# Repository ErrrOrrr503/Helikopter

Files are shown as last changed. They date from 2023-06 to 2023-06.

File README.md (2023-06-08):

# Helikopter
Еще один самособранный дрон. Цели: стабильный полет и потенциально большая грузоподъемность. Например, для поднятия фотоаппаруры.

# Комплектующие
Приобретались на aliexpress
* Рама: HSKRC XL9, карбоновая, X - образная


* Полетный контроллер: MATEKSYS H743-WING V2


* Контроллер двигателей ESC: Hobbywing XRotor Micro 60A 4 в 1 BLHeli-32


* GNSS & компас: MATEKSYS M10Q-5883


* Приемник и пульт: FLYSKY iA10B + FLYSKY i6x.


* АКБ: HRB LiPo 4S 3300mah 60C XT60, ширина ровно по раме.


* Винты: Карбоновые APC 1047, 10 дюймов хорошо встают не смотря на то что рама под 9 дюймовые


* Двигатели 2212 920KW


* FPV: 1200TVL камера + EWRF e708TM3 600mW передатчик + Skydroid 5.8G dual receier


* Шасси для F450 рамы: не использовалось, для XL9 слишком большое и тяжелое, использовались только углепластиковые трубки


* Провода 0.75 квадрата: соединение движков с ESC

* Провода ~3 квадрата: силовая проводка АКБ - ESC

* Тонкие провода в ассортименте

* Термоусадка в ассортименте

# Инструментарий
* 3D принтер Creality Ender 3 S1 Pro + PLA
* Паяльник
* Кусачки, отвертки и др. различный инструмент
* Прямые (мы надеемся) руки

# Проектирование

Для проектирования деталей использовались Solidworks и FreeCAD.
Проблем это как правило не составляло, за исключением 2х часов поиска причины не сходившегося чертежа из-за недоопределения вспомогательной геометрии.



# Изготовление

**Крепление камеры**

В комплекте рамы были приспособления для закрепления камеры. Однако в силу своей геометрии они не подходили к нашей камере. Поэтому для них была сделана замена. Точно подобрать размеры, чтобы крепления крепко зажималось но не оставляло зазоров получилось не сразу.



**Антенны**

Для закрепления антенн приема управляющего сигнала, передачи видеоизображения и антенны GNSS были изготовлены стойки. При их разработке ставилась задача максимально возможного удаления антенн друг от друга для снижения возможного взаимного влияния.





Первая версия крепления передатчика видео была спроектирована неправильно: вывод провода был с неправильной стороны - пришлось переделывать.

**Винты**

Имеющиеся двигатели и лопасти не подходили друг к другу. Большой проблемой было то, что диаметр отверстия лопасти был больше диаметра вала двигателя на ~0.2мм. Сделать втулку под такие размеры крайне проблематично. После исследования различных вариантов для ликвидации зазора была выбрана термоусадка. Процесс установки лопастей является относительно трудоемким для повторения и не был отснят, поэтому подробной фотографии нет.

**Пайка**

Довольно трудоемким был процесс разводки и пайки проводов для соединения компонентов между собой. Основную сложность составляли очень ограниченные размеры и геометрия, диктуемые рамой беспилотника.



**Программная часть**

В качестве прошивки используется Ardupilot c открытым исходным кодом. Ardupilot поддерживает используемый полетный контроллер, потребовалось только прошить бинарный файл во внутреннюю память. Ardupilot работает в паре с компьютерным ПО для настройки. Мы использовали MissionPlanner. Ardupilot имеет подробную документацию к настройкам и инструкции. Настройку можно производить в отведенных секциях или в сводной таблице параметров (там мы отключали логгирование т. к. иначе невозможен запуск без sd карты).



В пульте потребовалось инвертировать 2й канал т. к. движение вперед-назад было инвертировано.



**Шасси**
Все навесное оборудование расположено выше днища, так что без шасси можно было обойтись. Но в целях возможности размещения подвеса оно было сделано. Шасси съемное.



# Демонстрация

https://github.com/ErrrOrrr503/Helikopter/assets/55430721/89c44561-e986-4346-b0d1-1448f5957693

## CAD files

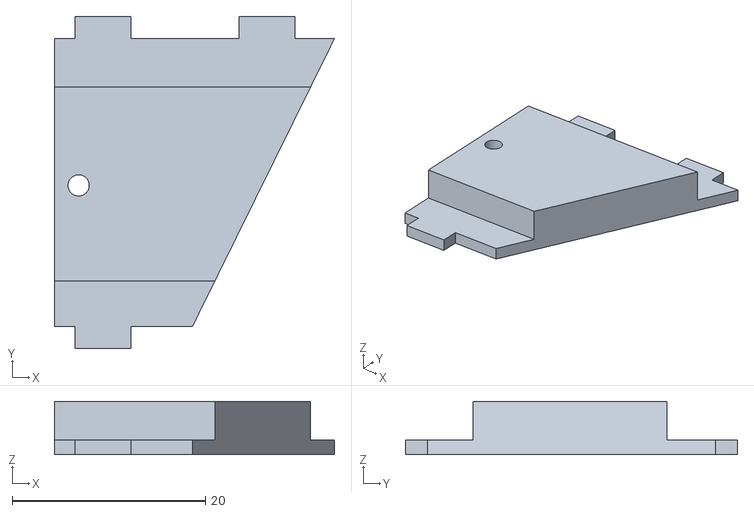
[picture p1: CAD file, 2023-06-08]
drafts/Cam_holder_right.stl
29.0 x 34.4 x 5.50

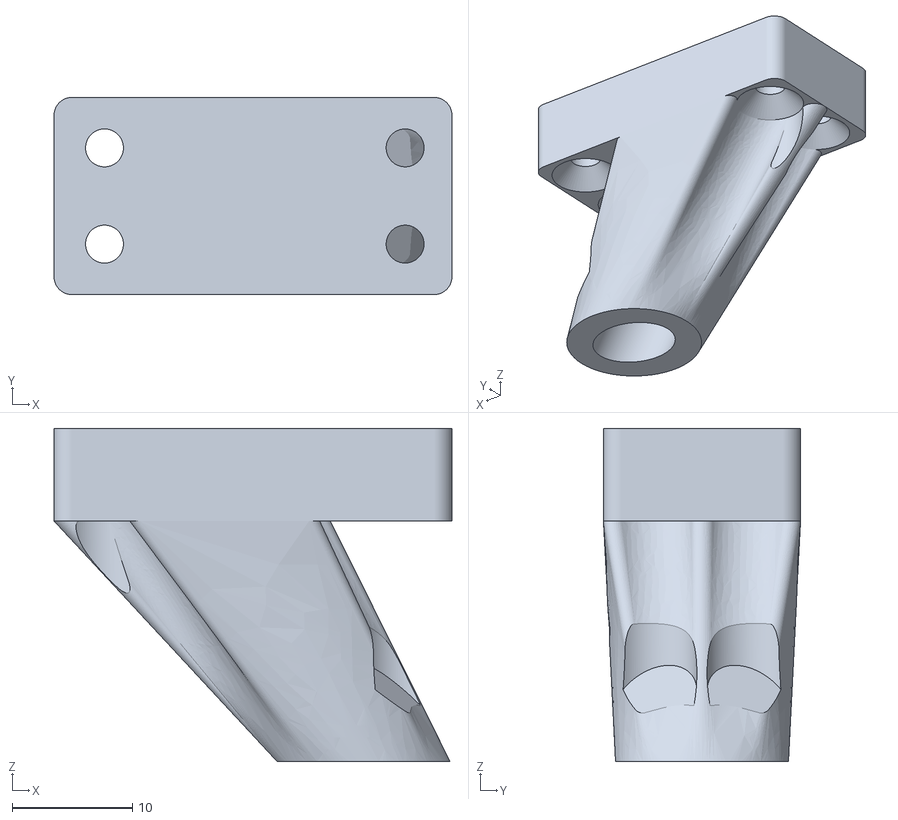
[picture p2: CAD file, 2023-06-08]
drafts/Leg_stick_holder.stl
33.1 x 16.4 x 27.7

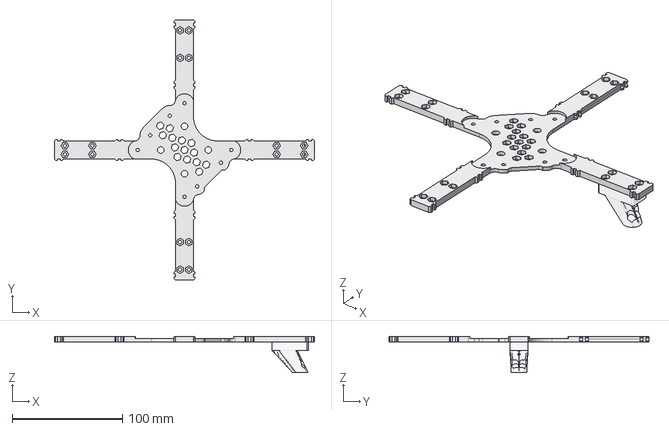
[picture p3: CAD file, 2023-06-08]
drafts/Leg_holder_bench.FCStd
236.0 x 236.0 x 32.7 mm

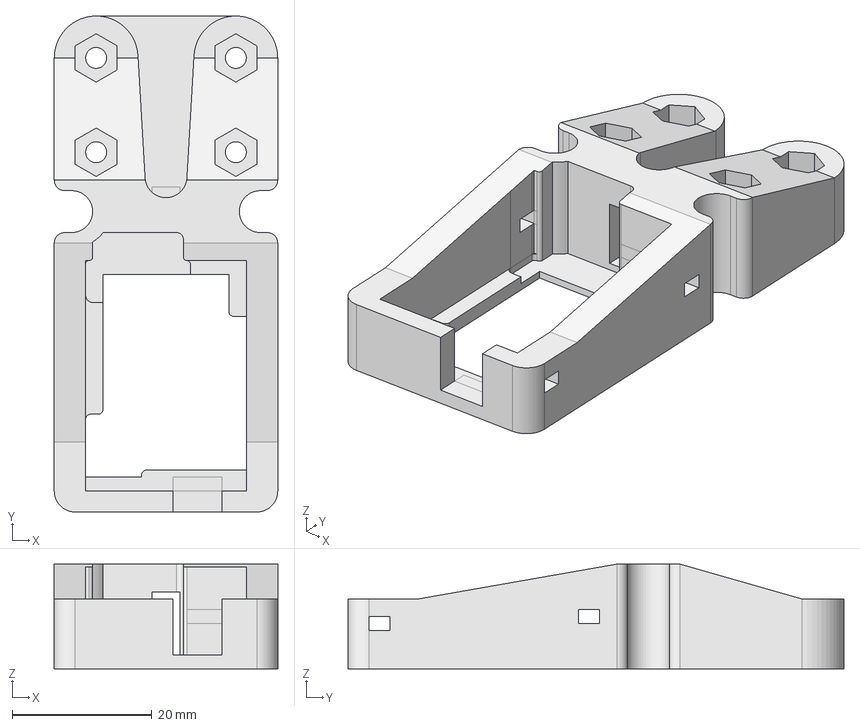
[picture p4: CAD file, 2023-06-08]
drafts/Video_transmitter_bench.FCStd
32.0 x 71.0 x 15.0 mm

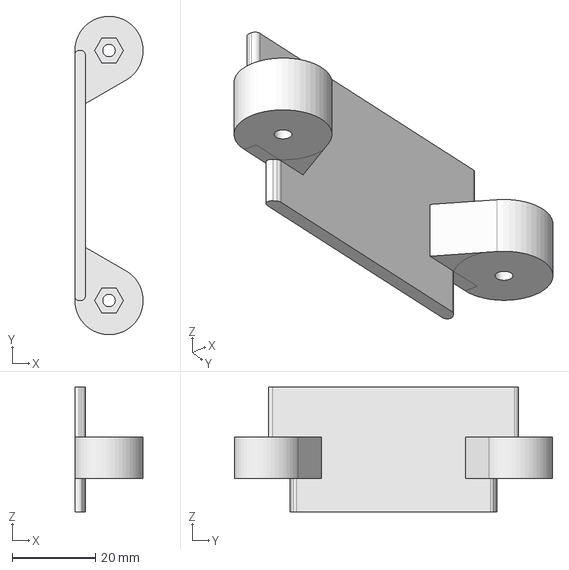
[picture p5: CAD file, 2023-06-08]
drafts/Recv_holder.FCStd
16.4 x 76.4 x 30.0 mm

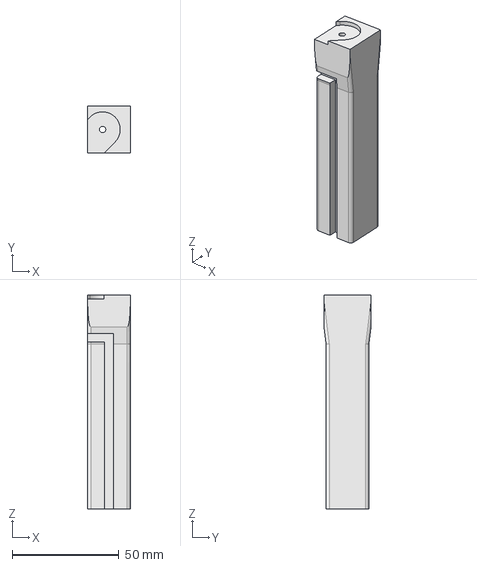
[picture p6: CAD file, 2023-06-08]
drafts/gps_bench.FCStd
20.0 x 22.0 x 100.0 mm

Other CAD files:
drafts/Cam_holder_left_edit.FCStd
drafts/Cam_holder_left.stl
drafts/Cam_holder_right_edit.FCStd
drafts/Leg_holder_bench.stl
drafts/Recv_holder.stl
drafts/Video_transmitter_bench.stl
drafts/gps_bench.stl

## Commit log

2023-06-08 drafts added
    [Cam_holder_left.stl, Cam_holder_left_edit.FCStd, Cam_holder_right.stl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]
2023-06-08 Update README.md
    Наведена Бюрократия.
